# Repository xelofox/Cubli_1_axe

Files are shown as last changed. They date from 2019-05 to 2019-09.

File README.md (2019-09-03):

# Cubli_1_axe
Guide d'implémentation de la commande d'un cubli 1 axe

Le projet était de continuer le travail effectué par un précédent groupe, il faut donc ajouter aux données ici les infos tirées de:
https://github.com/ABonnefoy/Cubli_ENS_Rennes

De plus les études qui ont motivés ce projet ainsi que leurs articles scientifiques sont retrouvables à:
http://www.idsc.ethz.ch/research-dandrea/research-projects/archive/cubli.html

Caractéristiques du prototype

Les caractéristiques du prototypes présentées sur le poster ont étaient déterminées de la façon suivante:

Les masses ont été déterminées en les pesant 

Le centre de gravité a été déterminé en accrochant le carré à un pivot et en mesurant l'angle de la diagonale par rapport à l'axe horizontal

Pour les inerties la méthode était géométrique: la masse volumique a été déterminé en relevant les dimensions et en considérant que la géométrie est la même que celle de celles des études des articles scientifiques (ce qui est le cas), les inerties en sont déduites (en prenant en compte les différences dans les dimensions).

Pour les coefficients de frottements, on a fait se balancer le carré et on a relevé la décroissance de ses oscillations qui évolue selon la constante de temps inertie/coeff de frottement. Pour le moteur on a fait de même en le faisant tourner à sa vitesse maximale au départ. Les observations ont était faites avec un logiciel de traitement d'image.

Ces caractéristiques sont retrouvables sur le script matlab Parametre.m.

Commande LQR 

La commande implémenter a été la même que celle des articles scientifiques, elle se retrouve aussi dans le script matlab à l'aide de la fonction LQR de matlab. Les coefficients de matrices Q et R peuvent être modifié à convenance en fonction de comment l'on veut que le système réagisse (violement ou lentement).

La modélisation avec l'application de la commande LQR est retrouvable sur le fichier simulink Modele17.slx

Le test de la récupération de la vitesse du moteur avec les sondes à effet Hall avec une utilisation du microprocesseur est disponible à Hall_CPU.slx .

L'implémentation à envoyer sur le microprocesseur est le fichier commandemoteur.slx, les pins à branchés sur la carte sont retrouvable dans la documentation de la carte (DAC etc).

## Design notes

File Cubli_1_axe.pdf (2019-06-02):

## École normale supérieure de Rennes | Département Mécatronique

Campus de Ker Lann - Avenue Robert Schuman - 35170 BRUZ – France

## www.mecatronique.ens-rennes.fr

# Asservissement d’un Cubli 1 axe

Détermination des paramètres mécaniques • Utilisation d’un codeur incrémental pour relever l’angle de la base: réglage mécanique pour l’alignement

## Essai de la commande sur un modèle simulink

Testard Nicolas, Stathopulos Alexandre, encadré par Roman Le Goff Latimier

## Réaliser la commande d’asservissement d’un cubli 1 axe afin qu’il tienne en équilibre sur un coin

2019

- L, Lb (longueurs indiquées sur le schéma)
- mb, mw (masse de l’ensemble et du moteur de la roue d’inertie)
- Ib, Iw (inerties de l’ensemble et du moteur)
- Cb, Cw (coefficients de frottement visqueux de la base et du moteur)

## Equations du mouvement

x l’état du système, u la commande: On cherche à minimiser la fonction:

Accouplement mécanique sur l’arbre et trous oblongs pour le support du codeur

Modèle simulink du cubli

Evolution de Theta_b, Theta_b’ et Theta_w’ après une perturabtion au cours du temps: ils tendent tous trois vers zéro

## Commande LQR du mouvement

Où Q et R sont des matrices dont les coefficients influent sur la réponse du
système (réactive si Q>R, économe si Q<R)

## Détermination de la vitesse du moteur avec des capteurs à effet Hall

-Un capteur permet d’obtenir la vitesse du moteur par la vitesse du champs magnétique rotorique -L’ajout d’un deuxième capteur permet de déterminer le sens de rotation

## Implémentation de la commande sur un microprocesseur par Simulink

-En entrée: les deux sondes à effet Hall donnant la vitesse et le sens de rotation du moteur, le codeur incrémental donnant directement la valeur de l’angle de la base (on en obtient la vitesse en intégrant) -En sortie: Le courant en entrée du moteur image de la vitesse, l’indication du sens de rotation du moteur pour le hacheur

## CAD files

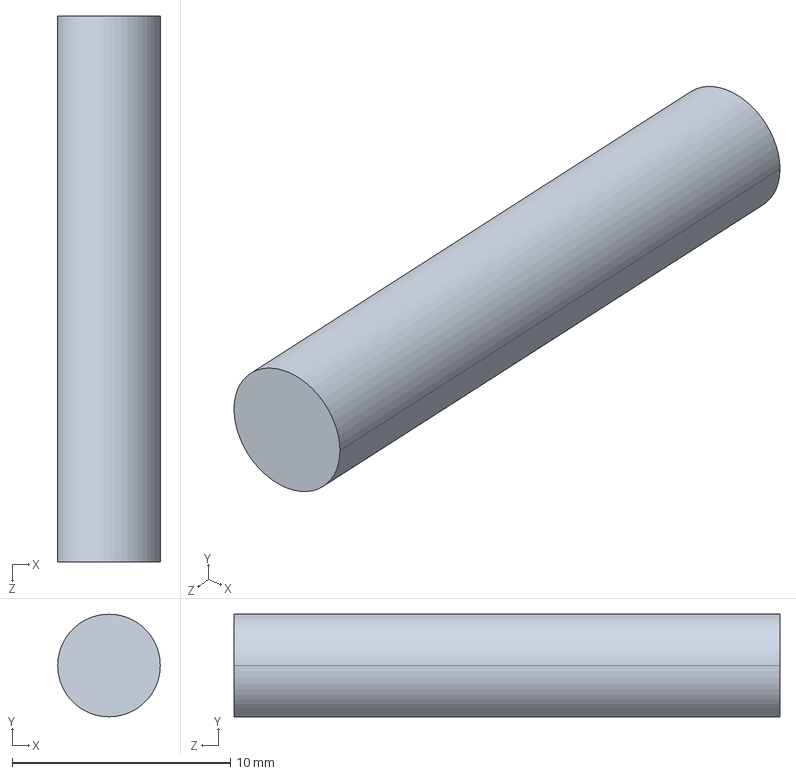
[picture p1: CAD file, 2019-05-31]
Pièces solidwork/barre codeur.STEP
4.70 x 4.70 x 25.0 mm

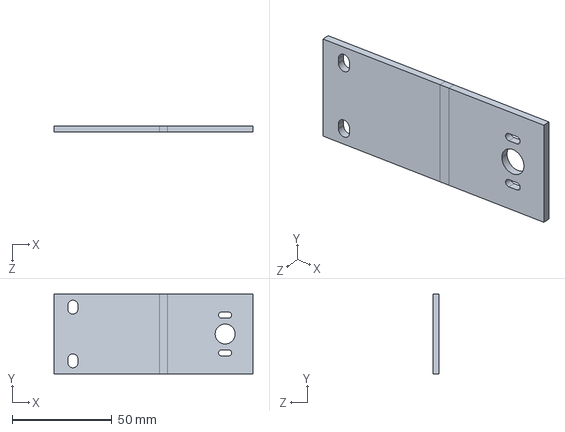
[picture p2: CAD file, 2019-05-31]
Pièces solidwork/support_codeur.STEP
100.0 x 40.0 x 3.00 mm

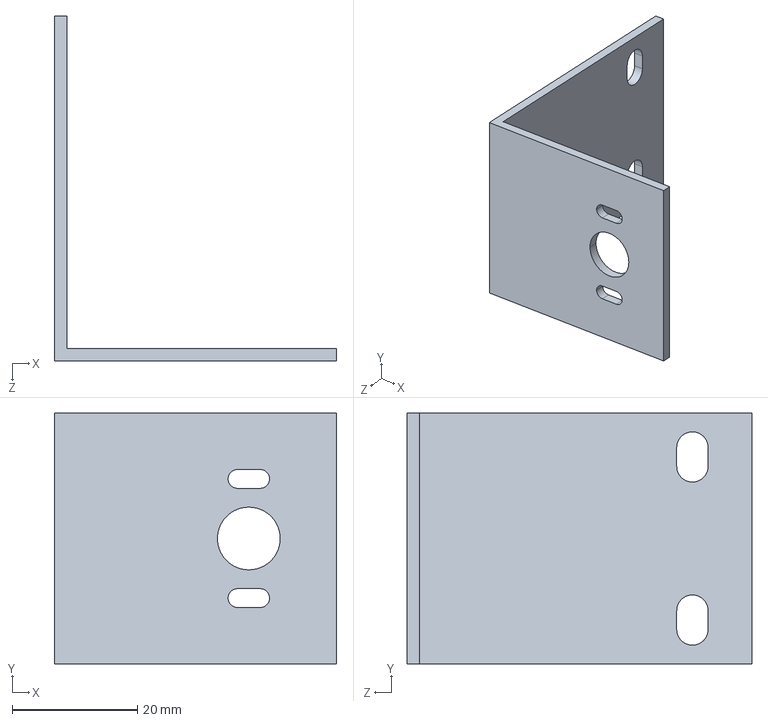
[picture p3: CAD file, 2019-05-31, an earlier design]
Pièces solidwork/support_codeur - Copie.STEP
45.0 x 40.0 x 55.0 mm

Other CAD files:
Pièces solidwork/barre codeur.SLDPRT
Pièces solidwork/support_codeur - Copie.SLDPRT
Pièces solidwork/support_codeur.SLDPRT
